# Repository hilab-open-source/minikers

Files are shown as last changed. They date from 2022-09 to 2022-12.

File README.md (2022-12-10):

# MiniKers: Interaction-Powered Smart Environment Automation

## About
MiniKers is a fleet of interaction-powered environment automation devices that harnesses energy from user interactions, achieving self-sustaining automatic operations that could last for long periods of time without human intervention (e.g., exchanging batteries). MiniKers system opens opportunities for turning user interactions into power sources for research in ubiquitous computing, IoT, and cyber-physical systems.

Please refer to the [paper](https://dl.acm.org/doi/10.1145/3550287) for more details.

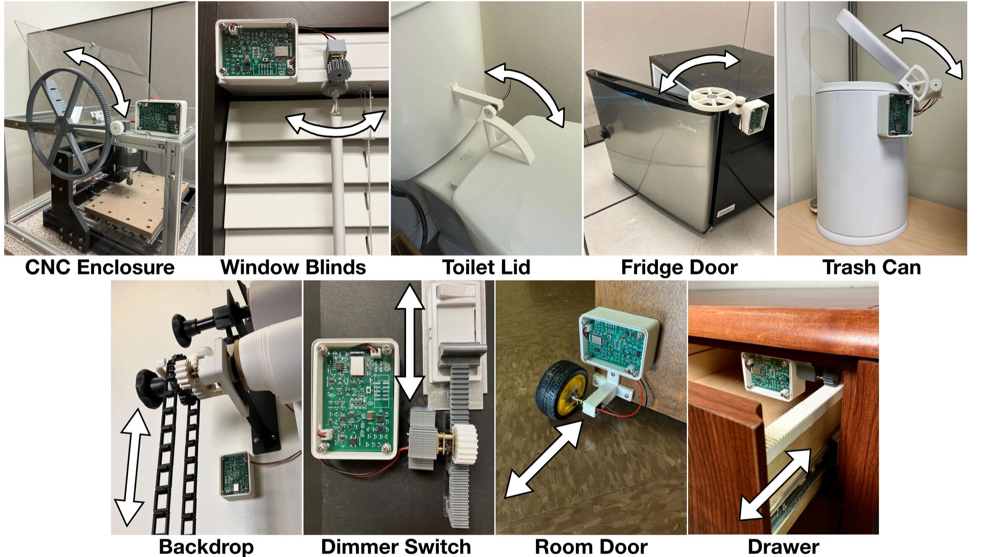
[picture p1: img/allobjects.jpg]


## Hardware
We designed a circuit to accomodate the manual and automatic operations of everyday objects. The circuit features a discharging and a charging mode to support the motor being used as either an actuator or a generator. It has a rechargeable supercapacitor and a Lithium-ion Polymer (Li-Po) battery. 

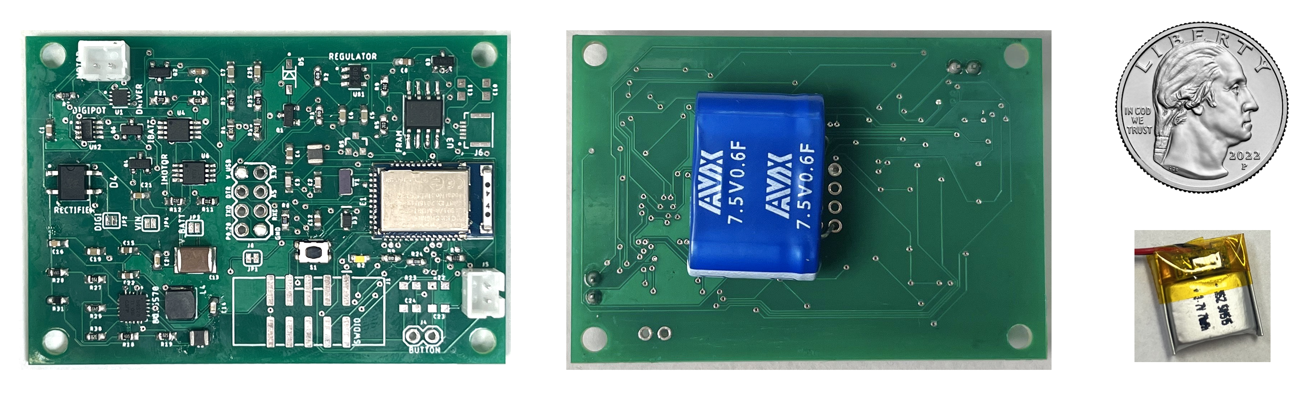
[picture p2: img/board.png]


## Contact
[info@hilab.dev](https://mail.google.com/mail/u/0/?fs=1&tf=cm&source=mailto&to=info@hilab.dev)

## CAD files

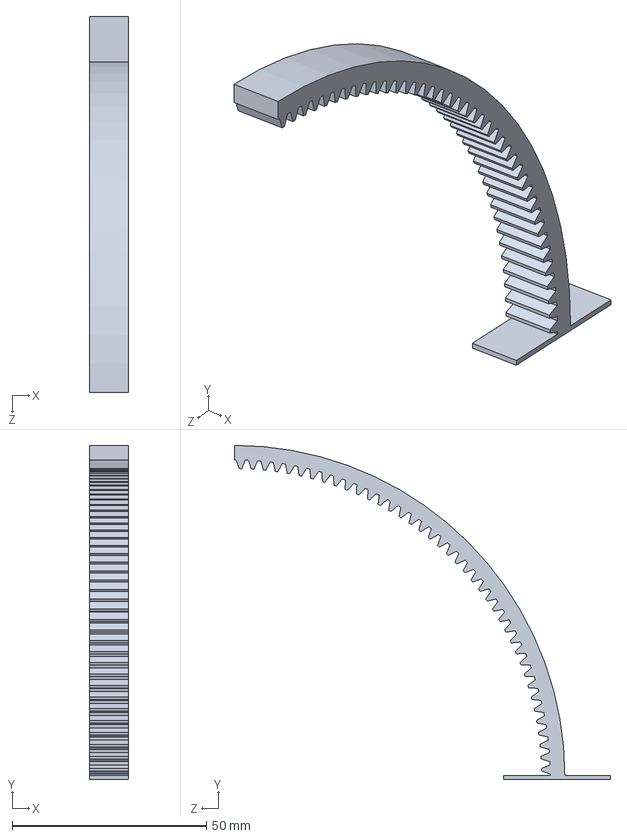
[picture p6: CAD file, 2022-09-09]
models/cnc-enclosure/inward gear (160 teeth).SLDPRT
10.0 x 86.0 x 96.7 mm

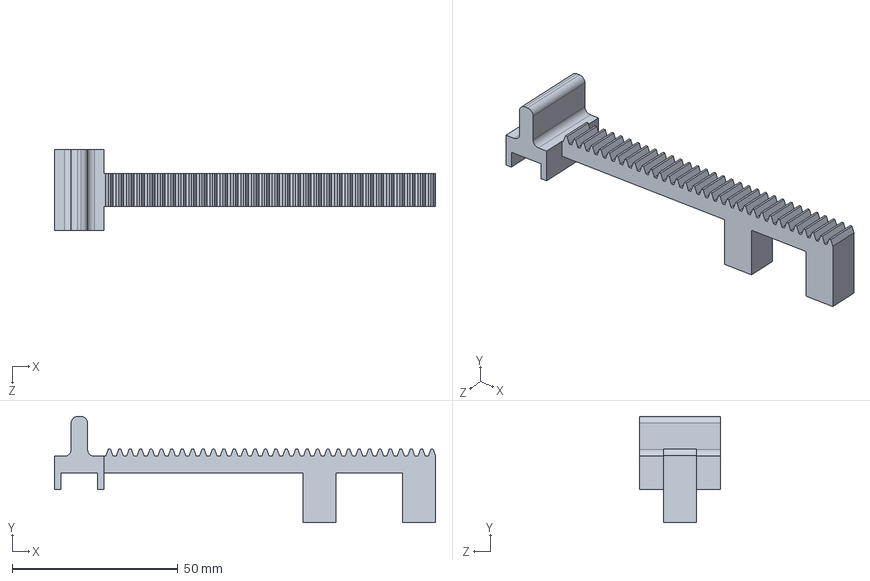
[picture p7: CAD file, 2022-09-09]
models/dimmer-switch/dimmer adjusted.SLDPRT
115.0 x 32.0 x 24.5 mm

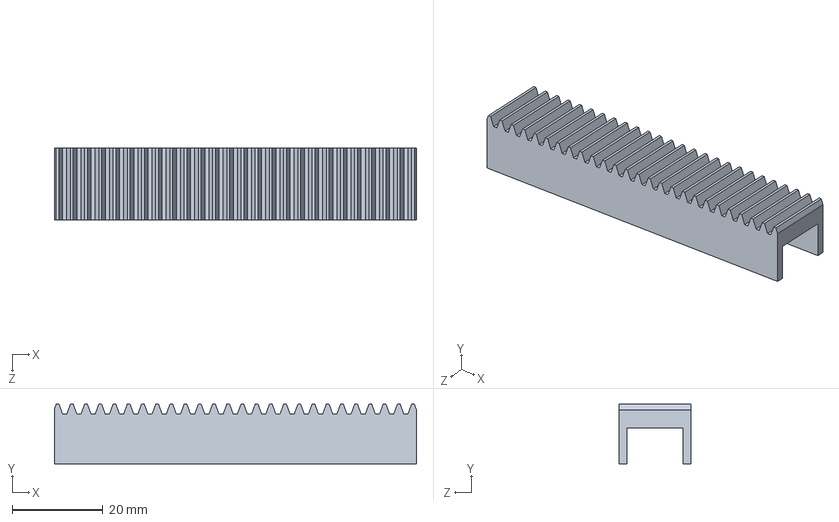
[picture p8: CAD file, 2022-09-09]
models/drawer-slides/pinion (height 5.25mm).SLDPRT
80.0 x 13.2 x 16.0 mm

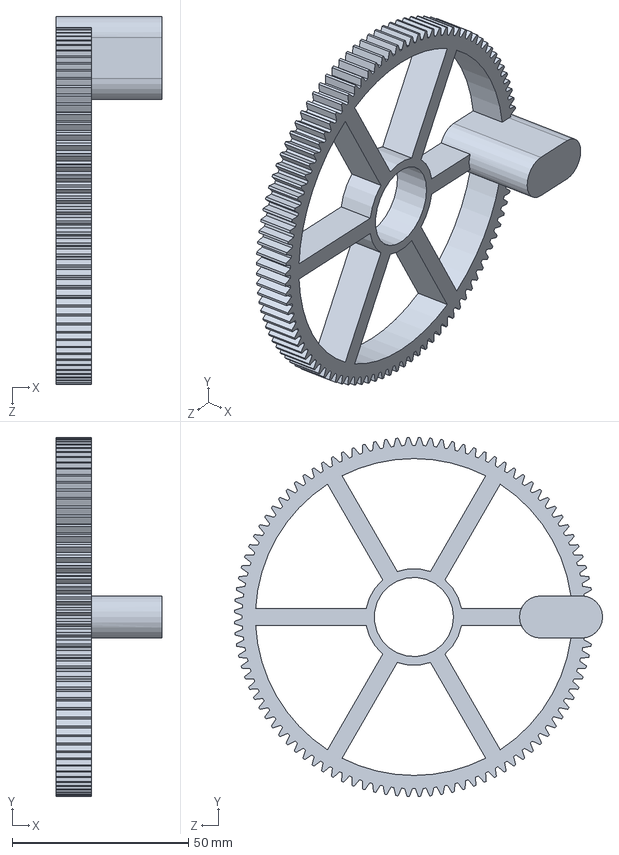
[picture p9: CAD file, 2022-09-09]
models/fridge-door/big (100 t).SLDPRT
30.0 x 102.0 x 104.6 mm

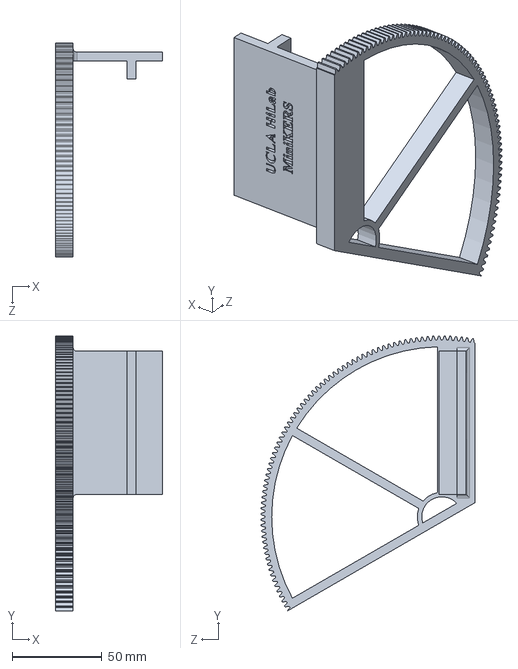
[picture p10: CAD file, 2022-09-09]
models/kitchen-cabinet/200 teeth.SLDPRT
60.0 x 153.5 x 119.5 mm

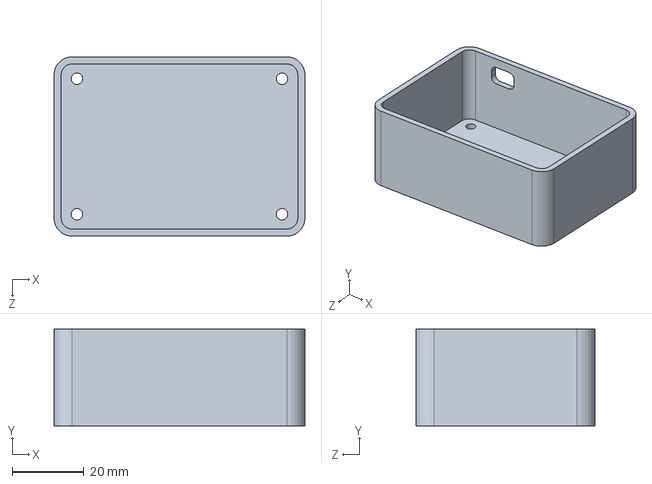
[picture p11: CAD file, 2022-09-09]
models/minikers-case/Acrylic.SLDPRT
70.0 x 27.0 x 50.0 mm

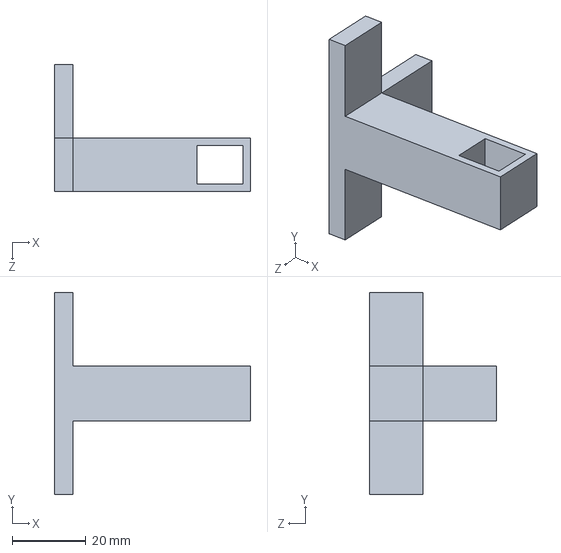
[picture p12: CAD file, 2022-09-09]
models/room-door/3 pronged mount.SLDPRT
53.2 x 55.0 x 34.5 mm

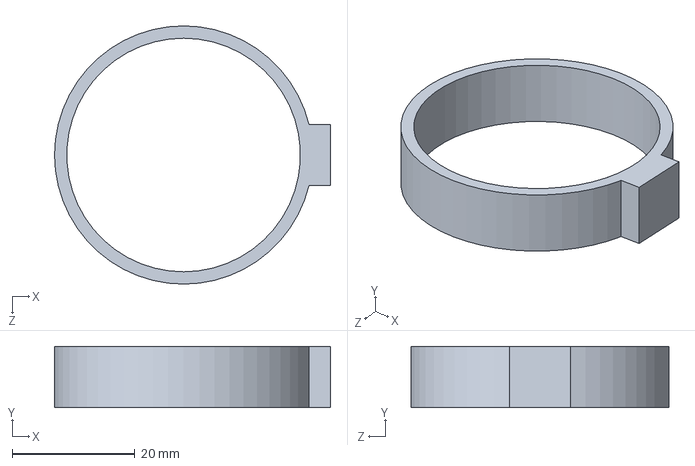
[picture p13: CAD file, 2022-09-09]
models/spray-bottle/circular holder.SLDPRT
44.9 x 10.0 x 42.0 mm

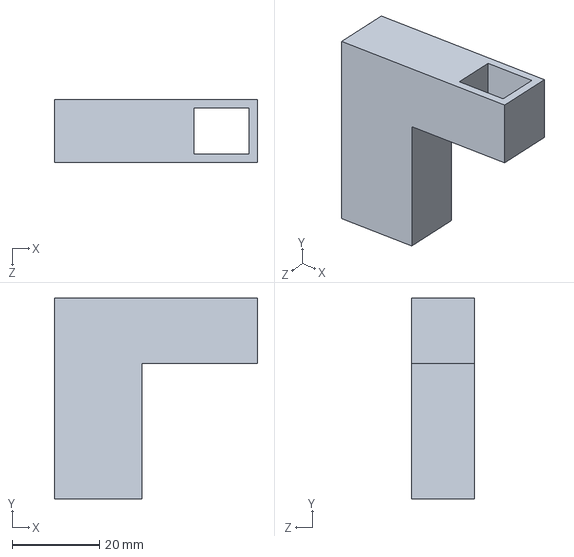
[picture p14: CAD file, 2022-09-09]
models/toggle-switch/toggle mount.SLDPRT
46.5 x 46.0 x 14.5 mm

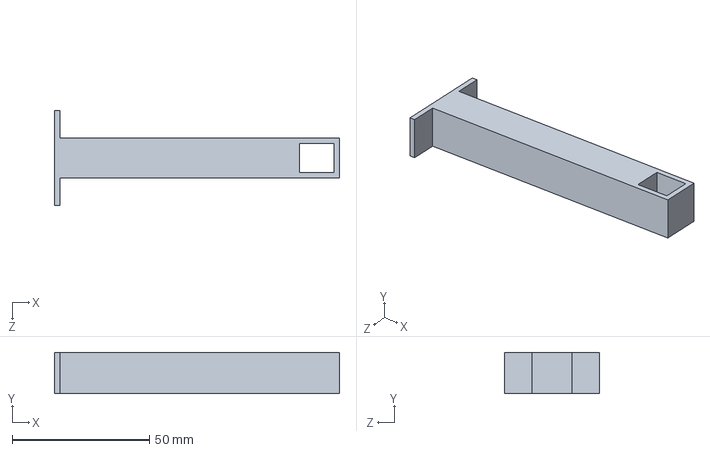
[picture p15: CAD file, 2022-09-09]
models/toilet-seat/mount.SLDPRT
103.8 x 15.0 x 34.5 mm

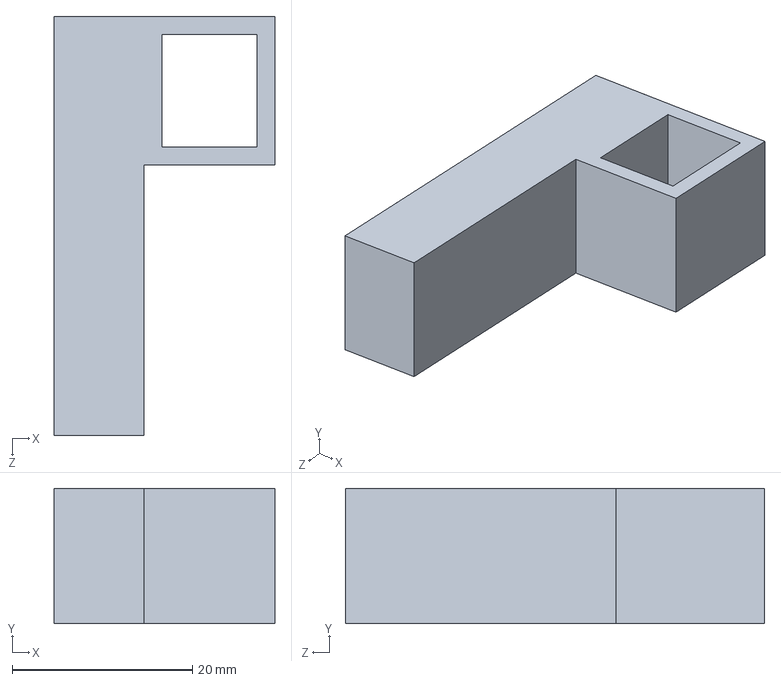
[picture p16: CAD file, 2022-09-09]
models/trash-can/trash bin mount.SLDPRT
24.5 x 15.0 x 46.5 mm

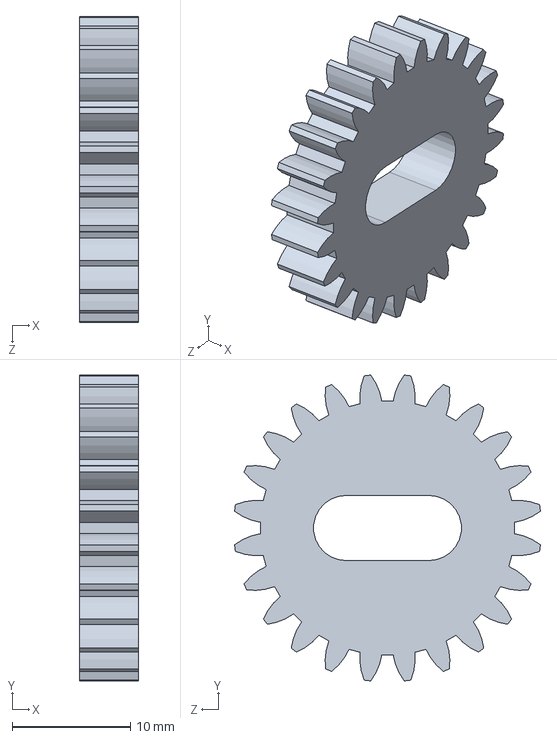
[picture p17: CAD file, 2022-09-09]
models/window-blinds/spur gear (24 t).SLDPRT
5.00 x 25.8 x 25.8 mm

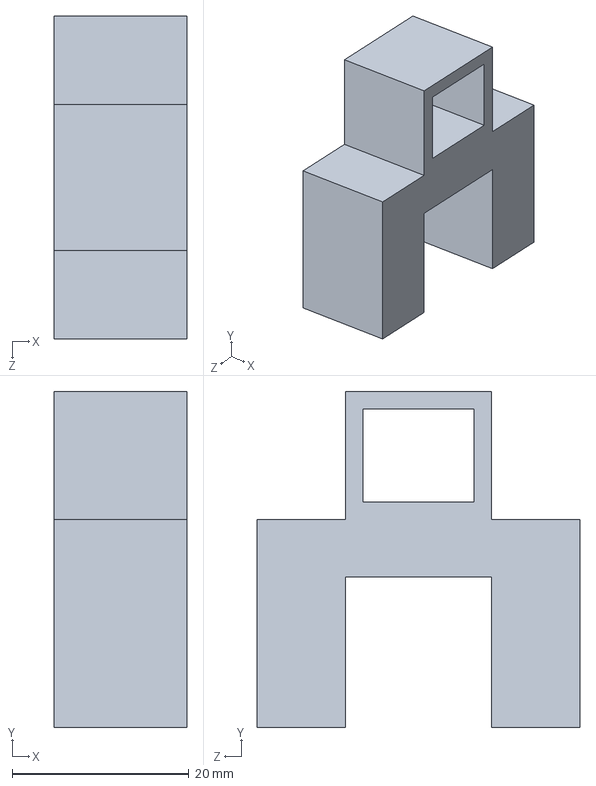
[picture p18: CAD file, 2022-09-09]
models/dimmer-switch/dimmer mount.SLDPRT
15.0 x 38.0 x 36.5 mm

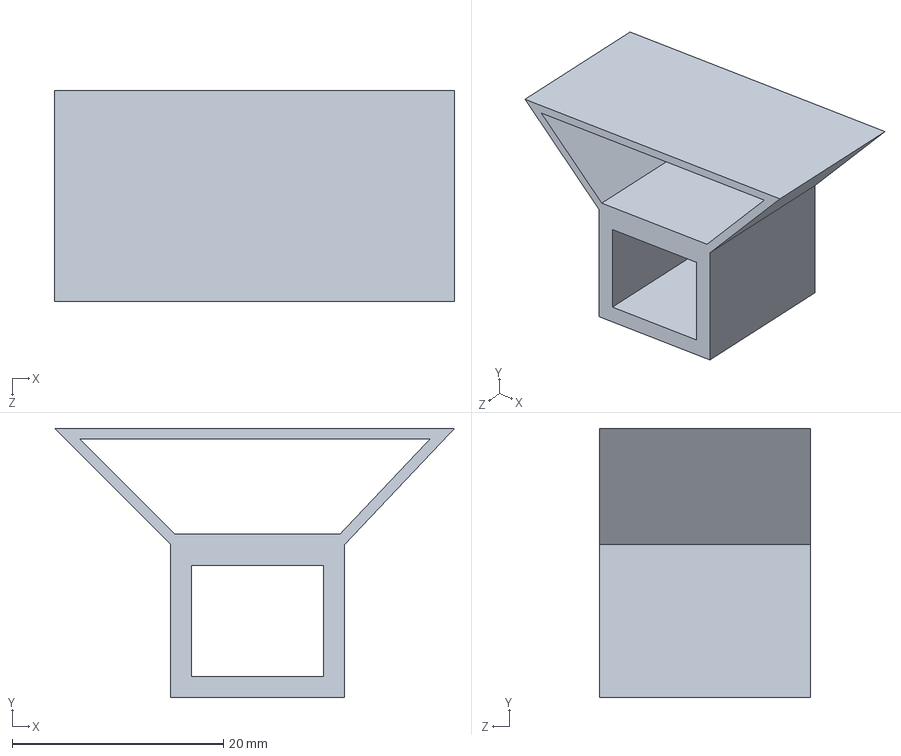
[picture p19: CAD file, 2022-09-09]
models/drawer-slides/motor mount (height 2mm).SLDPRT
37.9 x 25.5 x 20.0 mm

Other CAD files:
models/cnc-enclosure/inward gear (160 teeth) with support.STL
models/fridge-door/fridge mount.SLDPRT
models/kitchen-cabinet/plastic pin.SLDPRT
models/minikers-case/Acrylic Case.STL
models/cnc-enclosure/mount.SLDPRT
models/cnc-enclosure/mount.STL
models/dimmer-switch/dimmer adjusted.STL
models/dimmer-switch/dimmer mount.STL
models/drawer-slides/motor mount (height 2mm).STL
models/drawer-slides/pinion (height 5.25mm).STL
models/drawer-slides/spur gear (20 teeth).SLDPRT
models/drawer-slides/spur gear (20 teeth).STL
models/fridge-door/big (100 t).STL
models/fridge-door/fridge mount.STL
models/kitchen-cabinet/200 teeth.STL
models/kitchen-cabinet/plastic pin.STL
models/minikers-case/Acrylic.DXF
models/room-door/3 pronged mount.STL
models/room-door/mount.SLDPRT
models/room-door/mount.STL
models/spray-bottle/circular holder.STL
models/spray-bottle/dispenser mount.SLDPRT
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

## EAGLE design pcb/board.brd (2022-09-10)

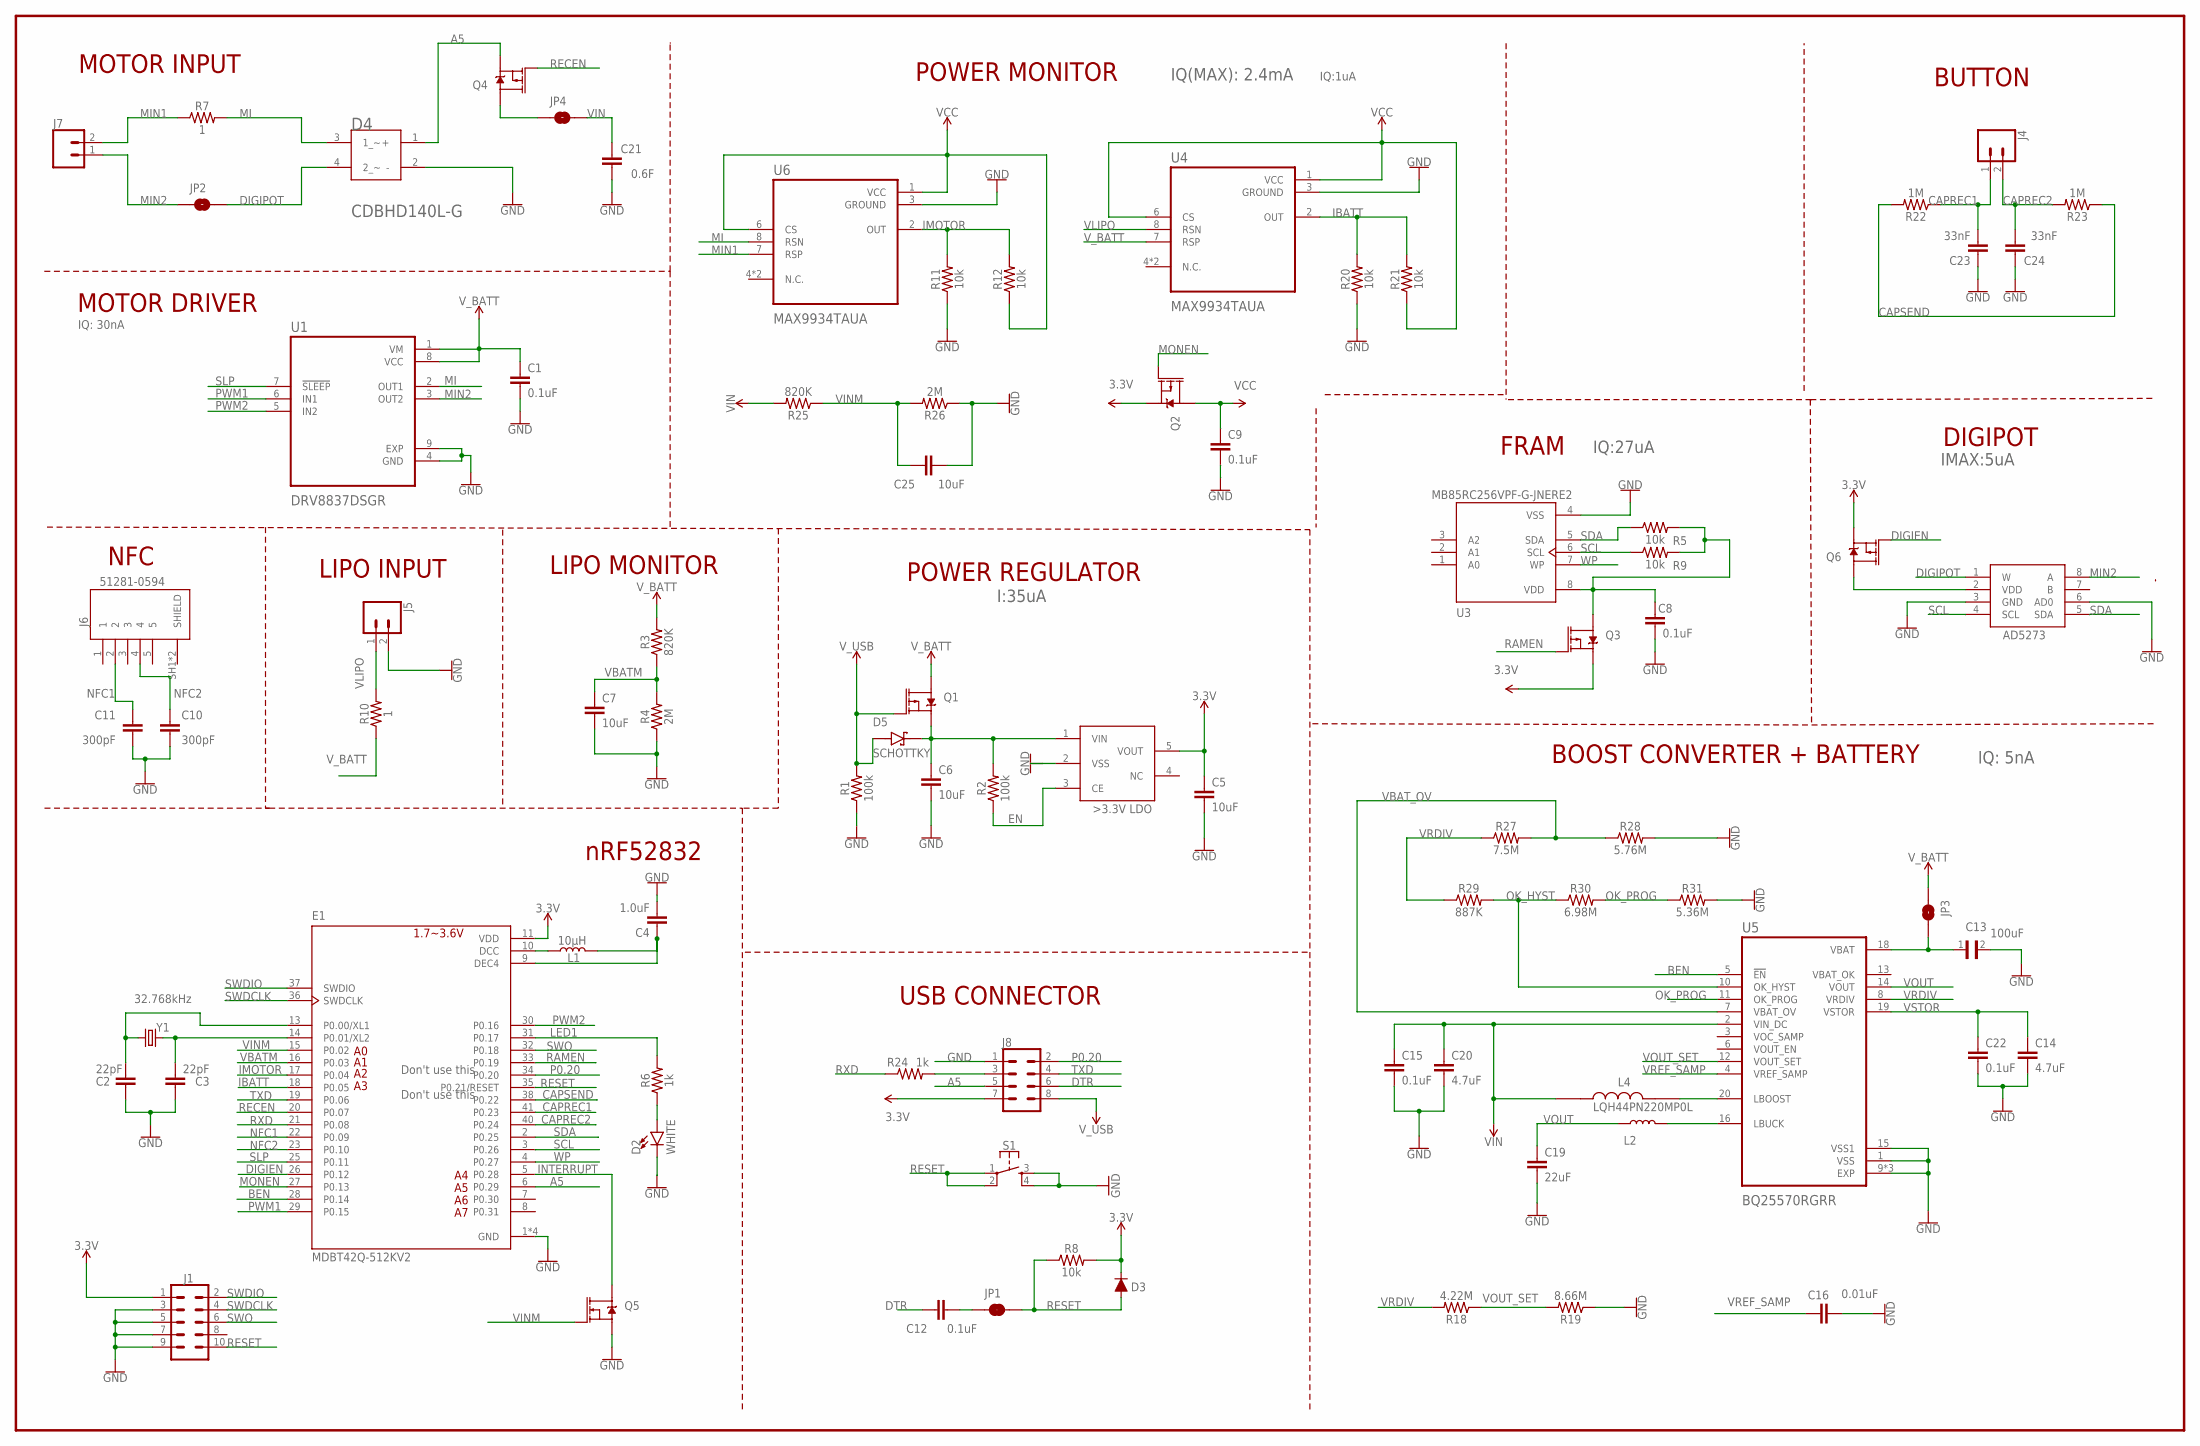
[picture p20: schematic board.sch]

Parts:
C1, C8, C9, C12, C15, C22: 0.1uF; 0603
C2, C3: 22pF; 0603
C4: 1.0uF; 0603
C5, C6, C7, C25: 10uF; 0603
C10, C11: 300pF; 0603
C13: 100uF; CAPC4532X127N
C14, C20: 4.7uF; 0805
C16: 0.01uF; 0603
C19: 22uF; 0603
C21: 0.6F; 0805
C23, C24: 33nF; 0603
D2: WHITE; LED-0603
D3: 250mA/100V; SOD-323
D4: COMCHIP_CDBHD140L-GCOMCHIP_CDBHD140L-G_0_0; COMCHIP_CDBHD140L-G_0
D5: SCHOTTKY; SOD3715X145N
E1: MDBT42Q-512KV2; RAYTAC_MDBT42Q-512KV2
J1: CONN_05X2SHD_SMD; 2X5-SHROUDED_SMD
J4, J5, J7: CONN_02; 1X02
J6: 51281-0594; MOLEX_51281-0594
J8: CONN_04X2; 2X4
JP1: JUMPER-SMT_2_NC_TRACE_SILK; SMT-JUMPER_2_NC_TRACE_SILK
JP2, JP3, JP4: JUMPER-SMT_2_NO_SILK; SMT-JUMPER_2_NO_SILK
L1: 10µH; 0805
L2: 10uH; 0805
L4: LQH44PN220MP0L; IND_LQH44PN220MP0L
Q1: MOSFET_PCH-DMG2307L; SOT23-3
Q2, Q3, Q4, Q6: 2.5A/30V/105mΩ; SOT23-3
Q5: 5.8A/30V/35mΩ; SOT23-3
R1, R2: 100k; 0603
R3, R25: 820K; 0603
R4, R26: 2M; 0603
R5, R8, R9, R11, R12, R20, R21: 10k; 0603
R6, R24: 1k; 0603
R7, R10: 1; 0603
R18: 4.22M; 0603
R19: 8.66M; 0603
R22, R23: 1M; 0603
R27: 7.5M; 0603
R28: 5.76M; 0603
R29: 887K; 0603
R30: 6.98M; 0603
R31: 5.36M; 0603
S1: MOMENTARY-SWITCH-SPST-2-SMD-4.6X2.8MM; TACTILE_SWITCH_SMD_4.6X2.8MM
U1: DRV8837DSGR; SON50P200X200X80-9N
U3: MB85RC256VPF-G-JNERE2; SOP127P797X210-8N
U4, U6: MAX9934TAUA; SOP65P490X110-8N
U5: BQ25570RGRR; QFN50P350X350X100-21N
U$1: IC_X8107AC20MR-GSMD; IC_XC8107AC20MR-G
U$2: AD5273; SOT65P280X145-8N
Y1: 32.768kHz; CRYSTAL-SMD-3.2X1.5MM

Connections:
3.3V: C5.1, D3.C, E1.11 (VDD), J1.1, J8.7, Q2.2 (S), Q3.2 (S), Q6.2 (S), R8.2, U$1.5 (VOUT)
A5: D4.1 (+), E1.6 (P0.29), J8.5, Q4.2 (S)
BEN: E1.28 (P0.14), U5.5 (!EN)
CAPREC1: C23.2, E1.41 (P0.23), J4.1, R22.1
CAPREC2: C24.2, E1.40 (P0.24), J4.2, R23.2
CAPSEND: E1.38 (P0.22), R22.2, R23.1
DIGIEN: E1.26 (P0.12), Q6.1 (G)
DIGIPOT: D4.4 (2_~), JP2.2, U$2.1 (W)
DTR: C12.1, J8.6
EN: R2.1, U$1.3 (CE)
GND: C1.2, C2.1, C3.1, C4.2, C5.2, C6.2, C7.2, C8.2, C9.2, C10.2, C11.2, C13.2, C14.2, C15.2, C16.2, C19.2, C20.2, C21.2, C22.2, C23.1, C24.1, C25.2, D2.C, D4.2 (-), E1.1 (GND), E1.12 (GND), E1.24 (GND), E1.39 (GND), J1.3, J1.5, J1.7, J1.9, J5.2, J8.1, Q5.2 (S), R1.1, R4.1, R11.1, R19.1, R20.1, R26.1, R28.2, R31.2, S1.3, S1.4, U1.4 (GND), U1.9 (EXP), U3.4 (VSS), U4.3 (GROUND), U5.1 (VSS), U5.9 (EXP), U5.15 (VSS1), U5.17 (EXP), U5.21 (EXP), U6.3 (GROUND), U$1.2 (VSS), U$2.3 (GND), U$2.6 (AD0)
IBATT: E1.18 (P0.05), R20.2, R21.2, U4.2 (OUT)
IMOTOR: E1.17 (P0.04), R11.2, R12.2, U6.2 (OUT)
INTERRUPT: E1.5 (P0.28), Q5.3 (D)
LED1: E1.31 (P0.17), R6.2
MI: D4.3 (1_~), R7.2, U1.2 (OUT1), U6.8 (RSN)
MIN1: J7.2, R7.1, U6.7 (RSP)
MIN2: J7.1, JP2.1, U1.3 (OUT2), U$2.8 (A)
MONEN: E1.27 (P0.13), Q2.1 (G)
unnamed: E1.10 (DCC), L1.1
unnamed: L4.2, U5.20 (LBOOST)
unnamed: C3.2, E1.14 (P0.01/XL2), Y1.P$2 (2)
unnamed: C4.1, E1.9 (DEC4), L1.2
unnamed: L2.2, U5.16 (LBUCK)
unnamed: C12.2, JP1.1
unnamed: C6.1, D5.C (K), Q1.2 (S), R2.2, U$1.1 (VIN)
unnamed: Q6.3 (D), U$2.2 (VDD)
unnamed: C13.1, JP3.2, U5.18 (VBAT)
unnamed: C2.2, E1.13 (P0.00/XL1), Y1.P$1 (1)
unnamed: C8.1, Q3.3 (D), R5.2, R9.2, U3.8 (VDD)
unnamed: JP4.1, Q4.3 (D)
unnamed: D2.A, R6.1
unnamed: J8.3, R24.2
NFC1: C11.1, E1.22 (P0.09), J6.2
NFC2: C10.1, E1.23 (P0.10), J6.4
OK_HYST: R29.2, R30.1, U5.10 (OK_HYST)
OK_PROG: R30.2, R31.1, U5.11 (OK_PROG)
P0.20: E1.34 (P0.20), J8.2
PWM1: E1.29 (P0.15), U1.6 (IN1)
PWM2: E1.30 (P0.16), U1.5 (IN2)
RAMEN: E1.33 (P0.19), Q3.1 (G)
RECEN: E1.20 (P0.07), Q4.1 (G)
RESET: D3.A, E1.35 (P0.21/RESET), J1.10, JP1.2, R8.1, S1.1, S1.2
RXD: E1.21 (P0.08), R24.1
SCL: E1.3 (P0.26), R9.1, U3.6 (SCL), U$2.4 (SCL)
SDA: E1.2 (P0.25), R5.1, U3.5 (SDA), U$2.5 (SDA)
SLP: E1.25 (P0.11), U1.7 (!SLEEP)
SWDCLK: E1.36 (SWDCLK), J1.4
SWDIO: E1.37 (SWDIO), J1.2
SWO: E1.32 (P0.18), J1.6
TXD: E1.19 (P0.06), J8.4
VBATM: C7.1, E1.16 (P0.03), R3.1, R4.2
VBAT_OV: R27.2, R28.1, U5.7 (VBAT_OV)
VCC: C9.1, Q2.3 (D), R12.1, R21.1, U4.1 (VCC), U4.6 (CS), U6.1 (VCC), U6.6 (CS)
VIN: C15.1, C20.1, C21.1, JP4.2, L4.1, R25.2, U5.2 (VIN_DC)
VINM: C25.1, E1.15 (P0.02), Q5.1 (G), R25.1, R26.2
VLIPO: J5.1, R10.2, U4.8 (RSN)
VOUT: C19.1, L2.1, U5.14 (VOUT)
VOUT_SET: R18.1, R19.2, U5.12 (VOUT_SET)
VRDIV: R18.2, R27.1, R29.1, U5.8 (VRDIV)
VREF_SAMP: C16.1, U5.4 (VREF_SAMP)
VSTOR: C14.1, C22.1, U5.19 (VSTOR)
V_BATT: C1.1, JP3.1, Q1.3 (D), R3.2, R10.1, U1.1 (VM), U1.8 (VCC), U4.7 (RSP)
V_USB: D5.A, J8.8, Q1.1 (G), R1.2
WP: E1.4 (P0.27), U3.7 (WP)

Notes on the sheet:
LIPO INPUT
nRF52832
LIPO MONITOR
POWER REGULATOR
USB CONNECTOR
MOTOR INPUT
MOTOR DRIVER
POWER MONITOR
BOOST CONVERTER + BATTERY
FRAM
DIGIPOT
1.7~3.6V
IQ:27uA
IQ: 5nA
IQ: 30nA
IMAX:5uA
IQ(MAX): 2.4mA
IQ:1uA
I:35uA
BUTTON
NFC
Don't use this

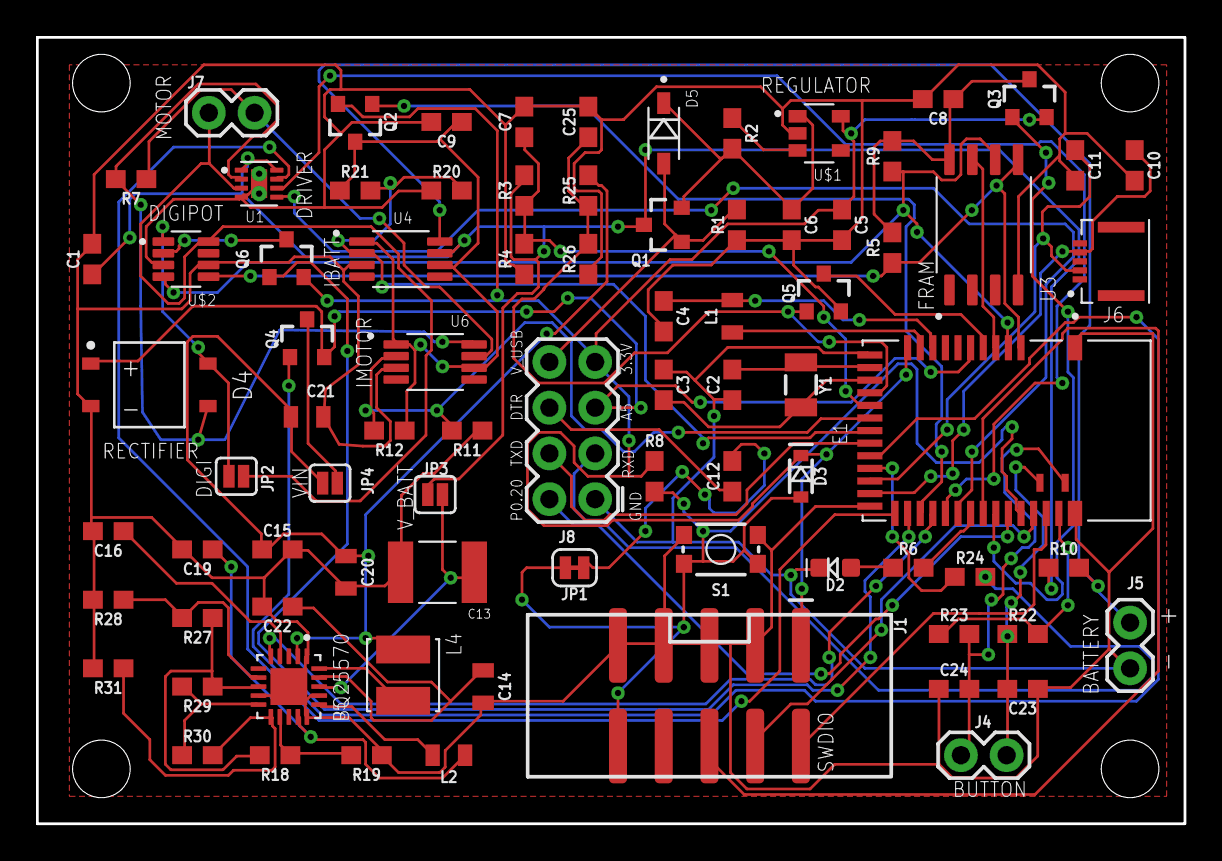
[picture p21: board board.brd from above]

Board: 2 copper layers, 63.8 x 43.7 mm, 82 parts (0 on the bottom side), 65 nets.

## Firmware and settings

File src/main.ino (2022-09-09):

#include "Arduino.h"
#include "Adafruit_TinyUSB.h" // for Serial

#include "initialization.h"
#include "fram_processing.h"
#include "motor_control.h"
#include "bluetooth.h"
#include "energy_control.h"
#include "time_setting.h"

void setup() {

//  Serial.begin(115200);
  
  PIN_SETUP();

  //BLE
  BLE_INITIALIZATION();

  // RTC
  RTC_SETTING();

  //SLEEP MODE
  //Bluefruit.begin();          // Sleep functions need the softdevice to be active.

  //DIGIPOT 
  //Wire.begin(); // join i2c bus

//  //FRAM
//  digitalWrite(DIGIEN, LOW);
//  digitalWrite(RAMEN, LOW);
//  FRAM_INIT();
//  FRAM_CLEAR();
//  FRAM_DUMP();

}


void loop() {

//  DATA_LOGGING();
  
  delay(100);

  unsigned long time_interval = millis() - manual_previous_time; 
  
  if (bluetooth_connected == false){

   PMONITOR(start_measuring, time_interval);

   CHARGING();

   STORE_DATA();

   SYSTEM_ON_SLEEP();
   
   BLE_PERIODICAL_ADVERTISE();
   
  }   

  else{
    
    digitalWrite(LED, HIGH);
    
    BLE_MODE(); 

    PMONITOR(start_measuring, time_interval);
    
  }

   manual_previous_time = millis();

}

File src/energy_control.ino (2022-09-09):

#include "initialization.h"
#include "motor_control.h"
#include "time_setting.h"



void manual_input_callback(){

  if (bluetooth_connected == false){

  digitalWrite(RECEN, LOW);

  manual_input = true;
  start_measuring = true; 

  // prepare data for writing to fram
  VIN_TO_SAVE = analogRead(PIN_UMOTOR) * VIN_DIVIDER * ADC_TO_V ;
  manual_start_time = rtc.now();

  //manual_previous_time = millis();
  
//  
//  while( start_measuring == true ){
//
////    DATA_LOGGING();
//
//    unsigned long time_interval = millis() - manual_previous_time; 
//
//    PMONITOR(start_measuring, time_interval);
//  
//    CHARGING();
//  
//    STORE_DATA();
//  
//    SYSTEM_ON_SLEEP();
//
//    manual_previous_time = millis();
//
//    delay(100);
//    
//  }
   
//  manual_count = manual_count + 1;   

  }
  
  else{
    digitalWrite(RECEN, HIGH);
  }

    
}

void PMONITOR(bool start_measuring,  unsigned long t) {

  if (start_measuring == true){
    
    digitalWrite(MONEN, LOW); 
   
    float VIN_ADC = analogRead(PIN_UMOTOR);
    VIN = VIN_ADC * VIN_DIVIDER * ADC_TO_V ;
  
    float VBAT_ADC = analogRead(PIN_UBAT);
    VBAT = VBAT_ADC * V_DIVIDER * ADC_TO_V;
  
    float IMOTOR_ADC = analogRead(PIN_IMOTOR);
    IMOTOR = (IMOTOR_ADC * ADC_TO_V - VBIAS) * A_TO_UA / ROUT_MOTOR / GAIN / SHUNT_R_MOTOR; //mA

    float PMotor = VIN * 0.001 * IMOTOR  ;
   
    
    if ( abs(IMOTOR) > MOTOR_RUNNING_THRESHOLD )
    {  
      motor_running = true;
    }
    else{
      motor_running = false;
    }

  
    float IBAT_ADC = analogRead(PIN_IBAT);
    IBAT = (IBAT_ADC * ADC_TO_V - VBIAS) * A_TO_UA / ROUT_BAT / GAIN / SHUNT_R_BAT; //mA

    float PBAT;


    if (charging_to_bat == true && IBAT > 0){
      PBAT = 0;
    }
    else{
        PBAT = VBAT * 0.001 * IBAT  ; // V * mA
    }
    
    EBAT = EBAT + PBAT * 0.001 * t; // J
  
    }

    else {
      digitalWrite(MONEN, HIGH); 
      
      EBAT = 0;
      IBAT = 0;
      IMOTOR = 0;

      motor_running = false;
           
    }

}


void CHARGING() {

  if (VIN > VIN_MAX_THRESHOLD ) {
    digitalWrite(BEN, LOW);
    charging_to_bat = true;

    // prepare data for writing to fram  
    charging_start_time = rtc.now();    
  }

  else if (charging_to_bat == true && VIN > VIN_MIN_THRESHOLD) {
    digitalWrite(BEN, LOW);
  }

  else { // VIN_MAX_THRESHOLD > VIN > VIN_MIN_THRESHOLD, charging_to_bat = false;

    digitalWrite(BEN, HIGH);

    if (manual_input == false){

       // prepare data for writing to fram  
      if (charging_to_bat == true){
        charging_end_time = rtc.now();
        writing_charging = true;
      }
      
      charging_to_bat = false;
      
      start_measuring = false;
      
    }
    
  }

    if ( manual_input == true ){
      
      digitalWrite(RECEN, LOW);
      
      if(motor_running == false){ // One manual input finished  
        manual_input = false; 
        pinMode(INTERRUPT_PIN, INPUT_PULLDOWN);

        // prepare data for writing to fram 
        
        manual_end_time = rtc.now();
 
        writing_manual = true;
       
      }
   }

    else{
            
      digitalWrite(RECEN, HIGH);
         
    }

    
}



void DIGIPOT(int R_limit) {

  digitalWrite(DIGIEN, LOW);

  Wire.beginTransmission(44); // transmit to device #44 (0x2c)
  // device address is specified in datasheet
  Wire.write(byte(0x00));            // sends instruction byte
  Wire.write(R_limit);             // sends potentiometer value byte
  Wire.endTransmission();     // stop transmitting

  delay(500);
}

void SYSTEM_ON_SLEEP()
{

  //LED that indicates the device is working
  if (SET_TIMER(LED_TIMER, led_previous_time) == true){
      digitalWrite(LED, HIGH);
      delay(50);
      digitalWrite(LED, LOW);
      led_previous_time = millis();
   }
   else{
      digitalWrite(LED, LOW);
   }

  // turn off all devices //low on high off

  digitalWrite(SLP, LOW);
//  digitalWrite(MONEN, HIGH); 
  digitalWrite(RAMEN, HIGH);  //---------------Attention: FRAM should be controlled by DIGIEN
//  digitalWrite(BEN, HIGH);
//  digitalWrite(RECEN, HIGH); 
  digitalWrite(DIGIEN, HIGH);
    
  //sd_app_evt_wait(); //System on sleep mode
  
}

void gotoDeepSleep(unsigned long time_)
{
  // shutdown when time reaches SLEEPING_DELAY ms
  if ((time_ > SLEEPING_DELAY))
  {
    Serial.println("Yes");
    // to reduce power consumption when sleeping, turn off all power hungry devices
    digitalWrite(LED, LOW);
    // turn off all devices in automation mode
    digitalWrite(SLP, LOW);
    digitalWrite(MONEN, HIGH); //low on high off
    digitalWrite(RAMEN, HIGH);
    // turn off all devices in manual mode
    digitalWrite(BEN, HIGH);
    digitalWrite(RECEN, HIGH);

    // setup wake-up pins.
    pinMode(WAKE_LOW_PIN,  INPUT_PULLUP_SENSE);    // WAKE_LOW_PIN is pulled up and wakes up the feather when externally connected to ground.
    //pinMode(WAKE_HIGH_PIN, INPUT_PULLDOWN_SENSE);  // WAKE_HIGH_PIN is pulled down and wakes up the feather when externally connected to 3.3v.

    //nRF5x_lowPower.enableWakeupByInterrupt(7, CHANGE);

    // power down nrf52.
    sd_power_system_off();  // this function puts the whole nRF52 to deep sleep (no Bluetooth). 600uA
    //If no sense pins are setup (or other hardware interrupts), the nrf52 will not wake up.
    //sd_power_mode_set(NRF_POWER_MODE_LOWPWR); // 600uA
    //sd_app_evt_wait(); //System on sleep mode
    //NVIC_ClearPendingIRQ(SWI2_IRQn);
    //__WFE();

    //suspendLoop();

  }
}

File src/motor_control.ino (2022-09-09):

#include "initialization.h"

 bool STALL_DETECTION(){
  bool stall_detected;
  if (abs(IMOTOR) > STALL_CURRENT){
    stall_detected = true;
  }
  else{
    stall_detected = false;
  }

  return stall_detected;
}


void MOTOR_RUN(int dir, float vel) {

  //Uncomment hardware pwm in setup()
  digitalWrite(BEN, HIGH);
  digitalWrite(RECEN, HIGH); //Low on, high off

  digitalWrite(SLP, HIGH);

  pinMode(PWM1, OUTPUT);
  pinMode(PWM2, OUTPUT);

  if (dir == 0) {
    digitalWrite(PWM1, LOW);
    //HwPWM0.writePin(PWM1, maxValue * vel, false);
    digitalWrite(PWM2, HIGH);
  }
  else {
    digitalWrite(PWM1, HIGH);
    //HwPWM0.writePin(PWM2, maxValue * vel, false);
    digitalWrite(PWM2, LOW);
  }
}
void MOTOR_BRAKE() {

  digitalWrite(SLP, LOW);
  digitalWrite(PWM1, LOW);
  digitalWrite(PWM2, LOW);

  //digitalWrite(LED, LOW);
  // turn off all devices in automation mode
  digitalWrite(MONEN, HIGH); //low on high off
  digitalWrite(RAMEN, HIGH);
  // turn off all devices in manual mode
  digitalWrite(BEN, HIGH);
  digitalWrite(RECEN, HIGH);

  pinMode(PWM1, INPUT);
  pinMode(PWM2, INPUT);
}

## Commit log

2022-09-09 ⚙️ Mechanisms
    [186 teeth double thickness.SLDPRT, 186 teeth double thickness.STL, 200 teeth.SLDPRT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]
2022-09-09 Add hardware files
    [board.brd, board.sch]
2022-09-09 Add board src
2022-09-10 Add board images
2022-09-10 🌠 Images
2022-09-10 💻 Source code
2022-09-10 👩‍🏭 PCB files
    [board.brd, board.sch]
2022-09-10 🧑‍💻 Source code

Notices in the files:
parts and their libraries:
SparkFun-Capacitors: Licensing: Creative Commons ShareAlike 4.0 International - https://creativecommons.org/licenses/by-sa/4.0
